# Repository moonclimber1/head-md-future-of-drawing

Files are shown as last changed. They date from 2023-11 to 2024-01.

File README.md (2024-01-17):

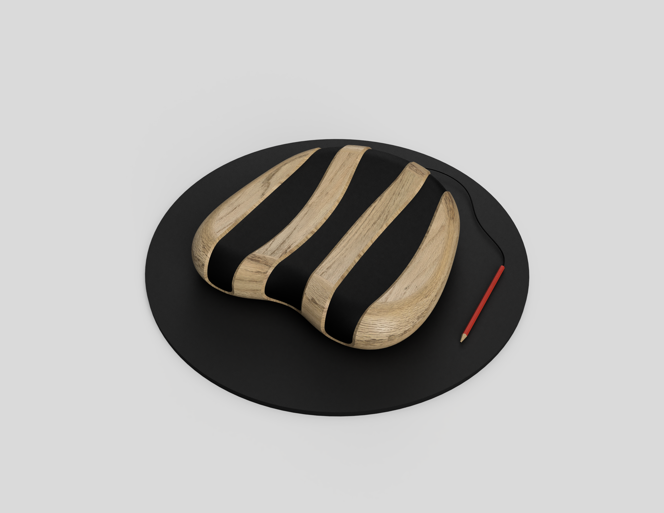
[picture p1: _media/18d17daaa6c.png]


# Future of Drawing

Github repository documenting process and code of the *Atelier Media Design 2023* at HEAD in which we explored possible Futures of Drawing in collaboration with Caran d'Ache.

[Overview of all projects of the class](https://github.com/HEAD-MasterMediaDesign/head-md-future-of-drawing)

## Shortcut Links

1. [Process Logs](process)  
   Logs every one or two working days
2. [To-Do-List](process/To-Do-List.md)  
   Current Tasks
3. [Presentations](presentations)  
   PDFs of all presentations did during the development process
4. [Form](form)  
   3D Renderings, Shape / Material experimentation
5. [Sound](sound)  
   Sound experimentations
6. [Electronics](electronics)  
   Arduino / Electronic diagrams and code
7. 

## Project Desription

**Resonance** -  Finding the inner balance through the movement of drawing

In the contemplative drawing experience Resonance people are  
encouraged to pause, slow down and enter a state of reso-  
nance - physically within the installation as well as metaphori-  
cally with themselves.

The core of the installation forms a novel interpretation of a  
sound bowl, crafted from wood and graphite. By engaging in  
slow rhythmic pencil movements on the object, people can set  
suspended pendulums in the space into gentle motion, creating  
contemplative soundscapes.

The rich electromagnetic properties of graphite are used to  
sense the rhythmic movement, allowing the pendulum to re-  
spond only when individuals move in resonance.

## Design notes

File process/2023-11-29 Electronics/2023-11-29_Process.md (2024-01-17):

# 2023-11-16 Process

## Electronics

In the last three days we had the electronics introduction with Pierre Rossel. We learned the basics of electronic circuits and arduino programming. After the obligatory basic examples of the first two days (dimming LEDs, potentiometer input, piezo, etc.) I started with my first own electronic experimentations today.

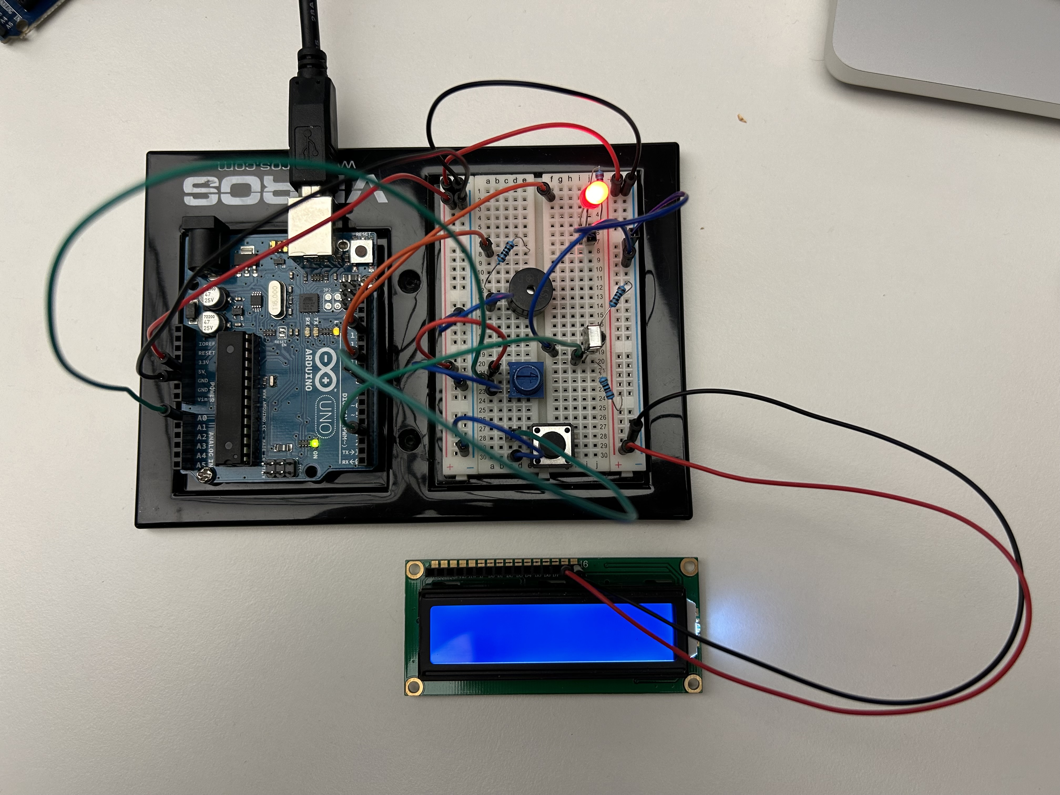
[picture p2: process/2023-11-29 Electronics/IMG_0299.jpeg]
Organized cable chaos on my breadboard
  
Organized cable chaos on my breadboard

Firstly I tried out different components of my arduino starter kit. I had an remote control and an infrared receiver and got them working together with the help of an downloaded online library. I made an setup in which I can remotely turn an LED on or off. Next I looked into the details how to get an display working. However as there is a lot of wiring up required (over 12 pins for my LCD display) I stopped with this endavour for time reasons. But at least I generally know how to do it in case I will need it.

**Video**  
[Video of LED Remote Control](IMG_0301.mov)

I wanted to move to doing actual experimentation that is related to my concept. After some wiring and tweaking I've got a resistance measurement on my pencil working. With this setup I am able to draw on a metal plate and it gives me the resistance value of the graphite which depends on the pressure. As a next step I created a TouchDesigner sketch to read the serial value and try around a bit with different signal processing options, e.g. applying lookup tables, filters, or lags. I achieved a setup in which I can control the brightness of my laptop screen just by changing the pressure with the pencil. The next step will be to use this improved clean signal to try to generate sounds. I started watching Max Msp Tutorial for synthesizer sound creations. With this setup I will hopefully soon be ready to do more user tests.

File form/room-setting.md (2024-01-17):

# Room Setting

**Carpet Measurements**

140cm x 130cm x 2cm

**Meditation Cushion**

35cm Diameter

17cm Height

**Projection Wall Distance**

1.7m Distance (equals 1.7m height)

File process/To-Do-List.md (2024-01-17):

# TODOs

## Current

**Object**

- [x] <span style="color:rgba(244,63,94,1)">Send improved 3D Model to Fred!</span>
- [x] <span style="color:rgba(244,63,94,1)">Send model to Laure</span>
- [x] <span style="color:rgba(244,63,94,1)">Produce Pencil Attachement</span>

  ***

- [ ] Prepare wood cover & holes for cables
- [x] Dremel missing cable channels
- [x] Sand edges
- [x] Glue parts together
- [x] Sand it
- [ ] Laquer it
- [ ] Sand strips
- [ ] Put graphite
- [ ] Cables (screws & routing)
- [ ] Put Electronics

**Room Setting**

- [x] <span style="color:rgba(244,63,94,1)">Design table & box</span>
- [x] Produce table
- [x] Produce equipment box
- [ ] Produce speaker stands
- [ ] (Design floating objects)

**Sound Design**

- [x] Check speakers & Interfaces
- [ ] Learn Ableton
- [ ] OSC Connection to TouchDesigner
- [ ] Create interactive soundscapes

**Visuals**

- [ ] Create Touchdesigner Visuals

**Presentation**

- [ ] <span style="color:rgba(244,63,94,1)">Deliver first version of presentation!</span>
- [ ] Define Framing!

**Electronics**

- [x] Fritzing wire diagram
- [ ] <span style="color:rgba(244,63,94,1)">Breadboard test</span>
- [ ] <span style="color:rgba(244,63,94,1)">Solder everything</span>
- [ ] Prepare for assembly

**Git Log**

- [ ] Look into git logs from class and last year
- [ ] Write more about design process / xylophone etc.

**Material to buy**

- [x] Clear lacquer / varnish spray
- [x] 6 nice screws for object
- [ ] (white wires?)
- [ ] female arduino connectors
- [x] Glue for cables
- [x] Round wood sticks

## Old

- [x] Research into different instruments (traditional, mechatronic)
- [x] Resarch into shapes (Exhibition tables, altar)
- [ ] sound design, electronics
- [x] metal workshop material measurement
- [ ] 3D Modeling
- [ ] form sketching
- [ ] try out lights

Define oscillating objects

- [x] research into different movement forms (springs, pendulum, unidirectional)

Define interaction & electronics

- [ ] usertesting
- [ ] Touchdesigner / P5 prototype

Think further

- [x] Think of flying object made out of paper (more related to drawing)
- [x] Email Audio Equipment
- [ ] Soldering excercise
- [ ] Try out Neopixel Rings
- [ ] Decide on camera model for documentation (sony pxw z150 vs canon 5D mark 4)
- [ ] ~~order pulleys~~
- [x] Frederic anschreiben
- [x] Pablo Audio Interfaces ausleihen & testen

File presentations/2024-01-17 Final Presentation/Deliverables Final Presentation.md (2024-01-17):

# Deliverables Final Presentation

Presentation until Wednesday

Fusion 360 File also until Wednesday

Github until Thursday morning

**General presentation**

November: What is the current state

January: -> This is the project!

Present as for someone new, but focus should lie on final product. 

Discuss process  but more as something that leads the way to the final product.

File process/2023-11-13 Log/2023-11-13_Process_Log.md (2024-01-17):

# 2023-11-03 Process Log

Today: Input with Laure, Brainstorming and discussions

After some discussion wth fellow students I feel the urge to revise my concept / experience again.

It might be more interesteing to focus on graphite as material in general instead of envisioning it in the form of a pencil.

Maybe create special analoge drawing devices that dont look an feel like penclis, maybe use eraser instead.

Maybe drawing with a pencil is too rigid for this contemplative experience, maybe graphite powder could be more interesting.

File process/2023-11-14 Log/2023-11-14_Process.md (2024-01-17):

# 2023-11-14 Process Log

I was not yet so happy with my concept and did a more research today and discussed the ideas with different persons.

My main problem was the following
“The more I add technological stuff the more it takes me away from being grounded ”

## Notes from discussion with Pablo

- There is nothing preventing you from being grounded if you do a simple interaction
- maybe also think of binaural sound via headphones instead of a big room setting
- do an simple satisfactory interaction that can help people relax and feel grounded  
  -> First goal: Relaxing people -> might eventually lead to being grounded
- finding inner balance through gesture of drawing
- constraining the movement you can do with a pencil might be interesting.
- #satisfaction: Inspired by wholesome videos that can help people relax
- Zen-like experience
- maybe draw in sand or graphite sand
- why do I want to use sound? -> it's an important aspect in relaxing people, immediate mental response
- feel good.
- also important to find sound references for the presentation

## New experiments

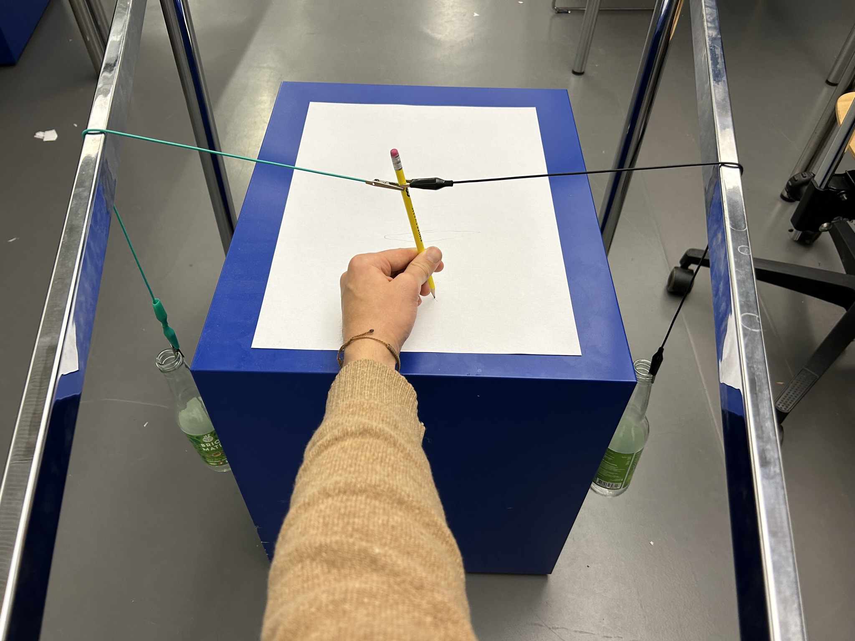
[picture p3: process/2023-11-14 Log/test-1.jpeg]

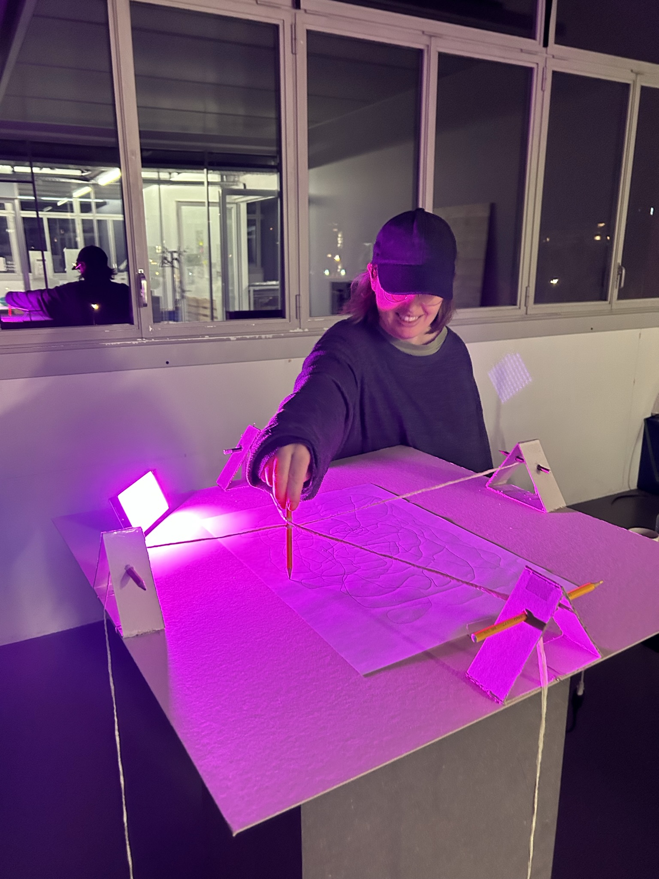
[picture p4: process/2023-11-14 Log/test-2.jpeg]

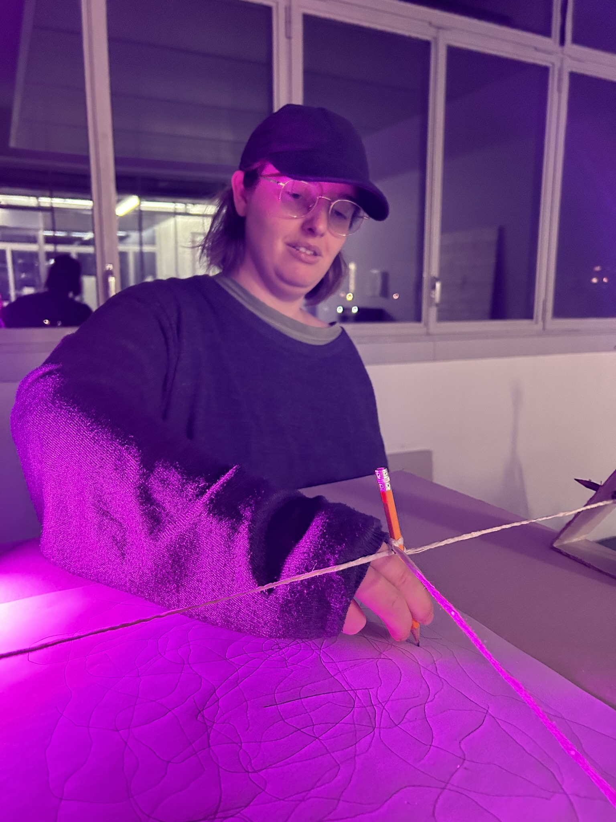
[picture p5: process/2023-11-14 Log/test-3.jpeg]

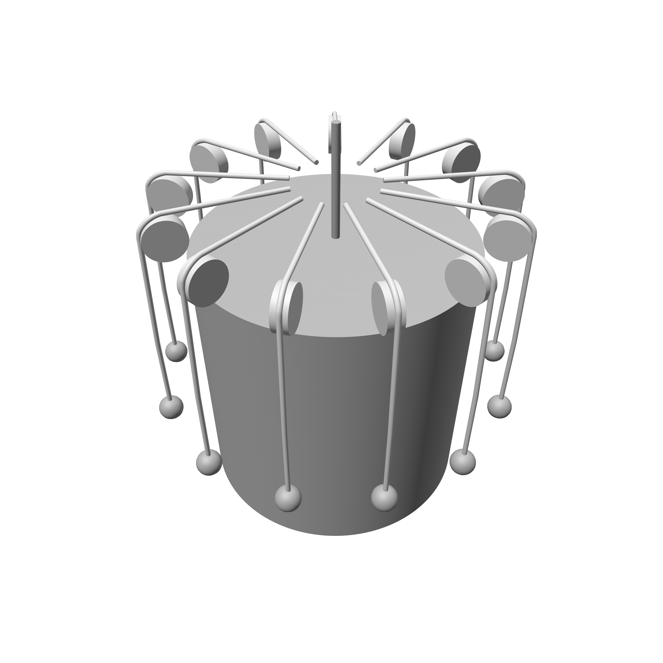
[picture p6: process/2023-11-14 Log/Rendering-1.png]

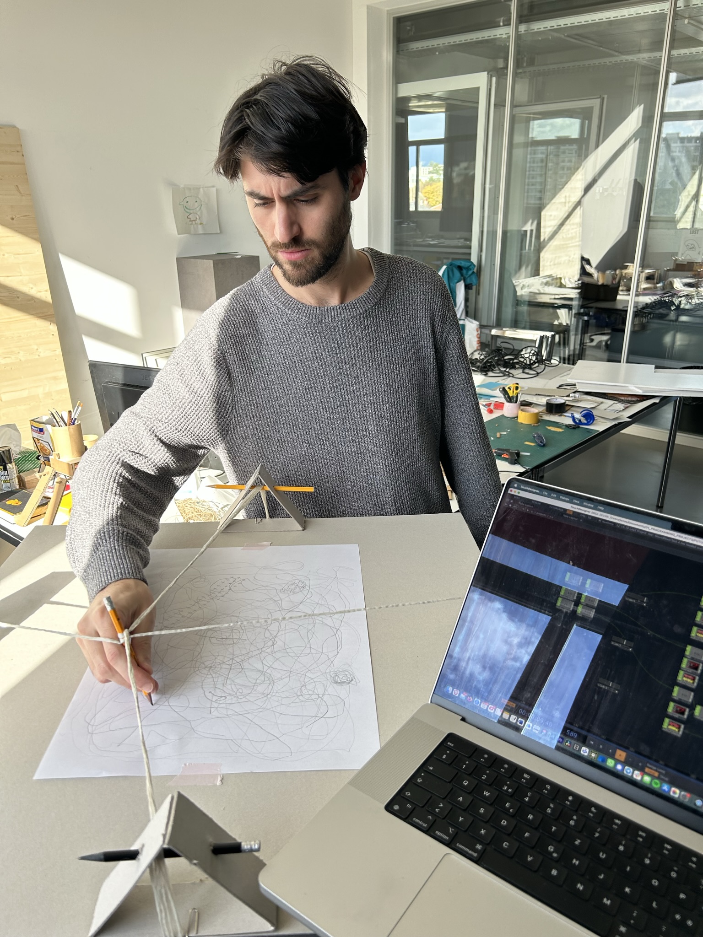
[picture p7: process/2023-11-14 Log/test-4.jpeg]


### Testing

People not only interact with the pencil directly but also try to pull on the ropes and draw indirectly over the mechanism.
Because of the big size of the object will probably also try to interact together with it.

I don't really want this indirect manipulation as it draws people away from what should be the focus. Maybe the ropes and stones have to be inside the table (behind a plexiglas) to not let people interact directly.

Through the constraints people are less likely to do figurative drawing, however they are strongly influenced about what has already been drawn. Ideally you wouldn't see a drawing on the paper and it would totally covered by graphite. Or you write on a metal plate.

## Updated Pitch

The project creates a multisensory contemplative drawing experience, with the goal of relaxing and centering / grounding people. They interact with an mechanical drawing object that at the same time gives constraints and sparks satisfaction through movement. While drawing, electromagnetic measurements of the graphite scratching on the the surface are measured and transformed into sounds that are altered by an AI to create looping spheric relaxing sounds. The installation creates a feedback loop in which the person influences the soundscape through their drawing movements while at the same time the sound influences their drawing.

There is an feedback loop between the object doing sound influencing the person and the person changing the sounds.

 you draw to create sounds while at the same time being influenced by the sonic expeirence and the Ai

In this manner a feedback loop is created

sparks satisfaction

designed to give constraint

an satisfactory experience

 an assists people in their groudning process. 

The pepople interact with an 

The drawing device is designed to makee people mre focus on the movemtents and have a visual feedback of the 

 make the the experience more satisfactory. 

cons

visitors interact with an satisfactory object while an AI creates sounds 

AI creates a sound that lets the come into resonance with their boday 

helping people to ground themselves and relax

helping people to find inner balance / center themselves / 

I wanted to design an object or experience that grounds people through the action of drawing.

There is an feedback loop between the object doing sound influencing the person and the person changing the sounds.

Where is the AI?

Finding resonance, findoing something that resonates with people

in the best case they get so focussed that they enter a meditative zone

binarual sound headphones

The project creates a multisensory wholesome / relaxing / contemplative drawing experience.

What is the title?

What is the core idea?

The project creates a multisensory contemplative drawing experience in which the electromagnetic traces of graphite are used to create a meditative, slowly pulsating painting of sound that gradually evolves in co-creation with an AI. The experience starts in a puristic setting of a dark room which floor is covered by water and only features a pencil hanging down from the ceiling and a blank canvas on the wall. Visitors have to enter barefoot and alone. Inspired by the slow rhythm of meditative breathing as well as the analogue richness of graphite, a pulsating and looping spheric soundscape starts to form as soon as the person begins drawing. Every drawn line contributes a sound to the evolving live loop while the AI is altering the past patterns with time. Visitors are encouraged to go with the flow as the emphasis shifts to the mental impacts of the act of drawing while the specific content of drawings becomes irrelevant.

Presentation peparation

- Go straight to the core of your project
- In interaction design you can not fake it last minute, you need to take your time and constantly test

This project is a ...

go straight to the point
put sentence of the end to the beginning.

help peole feel grounded

User Journey,

put pictures / vidoes of research / tests.

very simple shape research

if you have insights / discoveries from field reseach put those discoveries.

User tests: What worked?

go to very essence!

The testers expected…

First image: sketch, hand drawn.

Sound inspo
https://www.youtube.com/watch?v=8V71sATDTqs
https://www.youtube.com/watch?v=6BM-7oG1W6Y

## User Journey

1. Visitor gets curious about that special object.   

out of curiosity user wants to try out object 

User recognizes sound reactivity 

2. Visitor starts drawing with pencil and recognizes sound and watches rocks going up and down.
3. Visitor puts on headpohones and
4. 

is attracted by object and starts to try it ot

experiment of sound, graphite and metal (& movement)

pencil graphite loop

what gives it to me?

need an information

music is guiding me 
not enough guided

im getting into the flow
being out of sync

you have to get into their groove to get into your groove (like with a cat)

harmonics resonace is an interesting concept to be furter explored. Through drawing finding your resonance

rez game

can be honest about stuff Im not happy about yet, don't have to sell

its missng a conclusion, so what?

replace paper, put metal plate or dark paper. 

It need some kind of feedback, maybe get more into resonance 

talk shortly about voltage pencil experiment.

in the experiment

Is it more than just fun? Oh that's nice? What should stick?

It is an 

## Presentation notes

I was focussed on intensified sensory drawing experience and grounding people. as well as graphite 

talk about grounding research

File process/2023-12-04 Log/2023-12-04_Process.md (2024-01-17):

# 2023-12-04 Process

Today I further refined my concept. I had feedback discussions with Laure and Douglas as well as people of the class. 

## Discussion with Laure and Douglas

- Prototype is looking great, no need for the ropes (only if needed for the position, but there are probably better ways)
- Pencil pressure and drawing acts as a distortion to the sound
- around 4 instruments (e.g. gongs) hanging in the back, which are triggered by the movement of the pencil

- hanging things is hard, also think about other ways
- does it need to be a physical gong? It can be a modern interpretation of a gong, for example a physical object that resembles it while the sound is digital. Or just a specially formed resonance body for a speaker. Or cones, or a minimal paper shape, etc. 
- metal plate might have different zones for different sounds similar to DJ pults or drum machines. Zones might for example be achieved by thin laser engravings.
- A speaker with cones can already be very interesting, does not have to be a physical instrument. 

## New Inspiration

I discovered an artist called Lotta Stoever with interesting works which I found inspiring for my project.

https://lotta-stoever.net/works/towards-an-intimate-electricity

https://lotta-stoever.net/works/indisposable

## Temporary Materials List (rough)

- Instruments (Gong)
- Motors
- Metal Ropes
- Metal wheels
- Lights
- Microphone feedback

## Discussion with Ares

- currently difficult to decide what exact instruments I want to place with which visitor can inderectly interact with through the pencil movement
- I am missing one keyword that helps me connect the dots, to know better what I want as the output. Keyword might be something like "contemplative" or "oscillation" for example
- think also about big body movements
- doesnt have to be a horizontal metal plate on a table, can have any 3-dimensional form 

## Discussion with Laure

- maybe unidirectional drawing movement doesnt fit grounding experience so well
- think of more abstract objects going up and down, can be more poetic
- can also be a turning object or pendulum, or windmill like

## Next steps

I created a To-Do-List to track my progress and have an overview of my next steps:

[Link to To-Do-List](../To-Do-List.md)

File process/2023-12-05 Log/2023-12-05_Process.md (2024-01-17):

# 2023-12-05 Process

The interaction as well as the link to the "instruments" got much clearer today. I consider the keyword "Resonance" as the main keyword for the installation. "Resonance" can be interpreted in a metaphorical way, e.g. finding your inner resonance / get grounded as well as in a physical way for the interaction. Inspired by the mechanics of a pendulum or swing the goal is to make pencil movements in a specific rhythm to get into resonance with the oscillating floating objects which are hanging in the back. Similar to a physicial pendulum you can not just apply force at any time, you have to find the right moment to get the pendulum oscillating. The movement of the three pendulums will then influence the sound.

Resonance explained:  
https://www.youtube.com/watch?v=MIgQrHW53Lw

Example of dependence on the right rythm to get the pendulum into motion:
https://youtu.be/MIgQrHW53Lw?t=256

## Electronics Discussion with Pablo

- will neeed stepper motors with driver (never use the bad tb6600 model!)
- go at metal workshop and measure all kind of materials for different resistances
- maybe hack new carbon support printer
- cable thickness matters. when dealing with low voltages you have to be careful to no put to much current onto the cables. Check for max Ampere per length rating. Otherwise they will start burning.

## Discussion with Laure

- Circular movement is beautiful
- up and down movement is fluid as long it is on a big area, long plate might constrain this
- however circular movement maybe more difficult in terms of interaction
-

-
- light objects, like feathers, plastic foil, which make movements through going up and down and can also make waves if moved fast
- floating jellyfish
- rounded fluid forms

### How to find object design references online

- Pinterest & pinterest similar recommendations (maybe seperate account to train algorithm)
- if something sparks interest find out artist and search for more work of them
- Collection of interesting artists / design studios
- Wallpaper & Deezen Magazine
-
-

Ideas reasonating through light instead of movement

## Inspiration

Interesting kinetic light installation:
https://www.behance.net/gallery/141180655/Kinetic-Light-Installation

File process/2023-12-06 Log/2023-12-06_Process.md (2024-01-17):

# 2023-12-06 Process

made experiments with conductivity
carbonfiber plate experiment

electric field sensing

3D modeling & questions answers

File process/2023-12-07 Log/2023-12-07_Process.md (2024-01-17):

# 2023-12-07_Process

Douglas Testing Day Intro
Douglas Electronics Discussion

What I did:
- Electronics List, read into different technical topics to understand which exact components I need

Floating Objects Prototypes Results
- idea of having an inner glowing object and some kind of structure aroung
- the slow speed that I am targeting will not make plastic foil move on their own
- maybe strings attached to plastic foil
- maybe big paper wave or similar
- paper might still be interesting because of the relation to caran d ache

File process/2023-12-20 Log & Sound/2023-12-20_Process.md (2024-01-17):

# 2023-12-20 Process

Today I worked on the 3D Design of the product as well as organized sound equipment for january.

## Discussion with Laure about 3D Model

New inputs and references on how I can go for a warmer and more rounded form for the structure.  
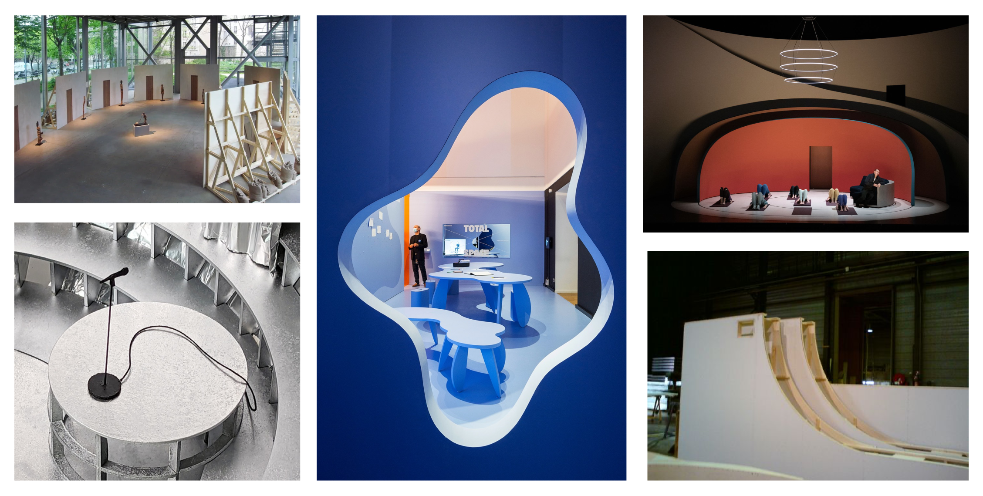
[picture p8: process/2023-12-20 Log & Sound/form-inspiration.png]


## Sound Equipment

Asked for sound equipment in pool image son. Difficult situation as there are jury presentations at the same time in January.

I reserved the following items in de magasin audiovisuel:

- 3 Fostex Speakers starting from the 10th of January
- Cameras (either sony pxw z150 or canon 5D Mark IV) starting from 16th of January for Documentation + Canon 16 -35mm lens	

Speaker stands still unclear

For the sound cards I might combine two sound cards from Media Design. Have to test how well that works.

granular synthesis

either only max msp + vsts

sampler, granular, synth, sample-based

VST: Noire grand piano (Native instruments)

note 1-12 or note 1-24 (maybe multiplied or add 12)  
first generating random node, and then use scale

Slide AI for May

note in chromatic scale  
random within a collection of possible scale

anneroli

put keyboard on computer

some things evolve over time

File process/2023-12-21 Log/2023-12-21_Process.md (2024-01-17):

# 2023-12-21 Process

## Feedback Laure Douglas

back to the basics  
graphite plate is the important thing.  
Too much structure draws away from the center of the poetic interaction.

projection as a plan B if physical movement doesnt work out until January presentation

Focus more on Design of the interaction plate object! Its at the center of my project and corresponds more to what others are doing as well.  
Get this object poetic in itself

pencil design second / third priority

paper is nice as floating object

arms that go up and down probably much better than undwindig. Also has poetry to it

Xylophone: Put two sticks below and its already regarded as a xylophone I can play with.

its nice to see cables and also nice to see inside

Prototype Plate is beautiful!

box design not ideal, same as with structure. It draws away from the poetics, feels not inviting enough to interact with.

Get rid of structure again. Mount all motors up to the ceiling.

Inspiration Alexander Calder  
Zimoun / Pelong Ref

why not go about projection

They are happy with paper material of floating object

In case of the floating objects, nice floating is more important than the look, therefore its good to test out material first and then do the form.

Plexiglass see through

maybe even make electronics / arduino visible with a little light? maybe too much? How technical I want it to be?

has to be discussed how importan ergonomics really are.

Critique current interaction console: You would no put your hand ther while drawing. It has to be the big angled plate / table so it works

maybe visible cable connection to object?

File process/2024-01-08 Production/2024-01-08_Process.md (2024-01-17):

# 2024-01-08 / 09 Process

Morning Appointment with Frederic in the atelier prototypage for the CNC. He will be able to produce the object but unfortunately only short before the presentations.

## CNC Specifications

- 4cm maximum piece height
- 4cm means a minimum radius of 3mm when doing concave edges
- I will have to cut my object into pieces, as the CNC only works on 3 axis
- 12mm distance between objects, 5mm to the edges
- Max working area 1000mm x 500mm
- one round drilling tool and one flat tool
- if its only on the surface its possible to work with thinner tools

## Work

3D Modeling & Troubleshooting with Laure

Wood workshop organizing

Wall projection test

## Wood Choices

Volume for CNC: 412mm x 824mm x 43mm = 1'4597'984 mm3 = 0,014 598 m3

**Wood Options**

| French | German | English  | Hardness | Price m3 | Object Price |
| --- | --- | --- | --- | --- | --- |
| <span style="color:rgba(156,163,175,.8)">Epicéa</span> | Fichte | Spruce | Soft | 1782 | 26 CHF |
| ~~Pin~~ | ~~Kiefer~~ | ~~Pine~~ | Soft | | |
| Hêtre | Buche | Beech | Hard | 2558 | 37.35 CHF |
| Erable | Ahorn | Maple | Hard | 3218 | 46.97 CHF |
| **Frêne** | Esche | Ash | Hard | 2558 | 37.35 CHF |
| Chêne | Eiche | Oak | Hard | 3713 | 54.20 CHF |

**Hêtre - Beechwood**

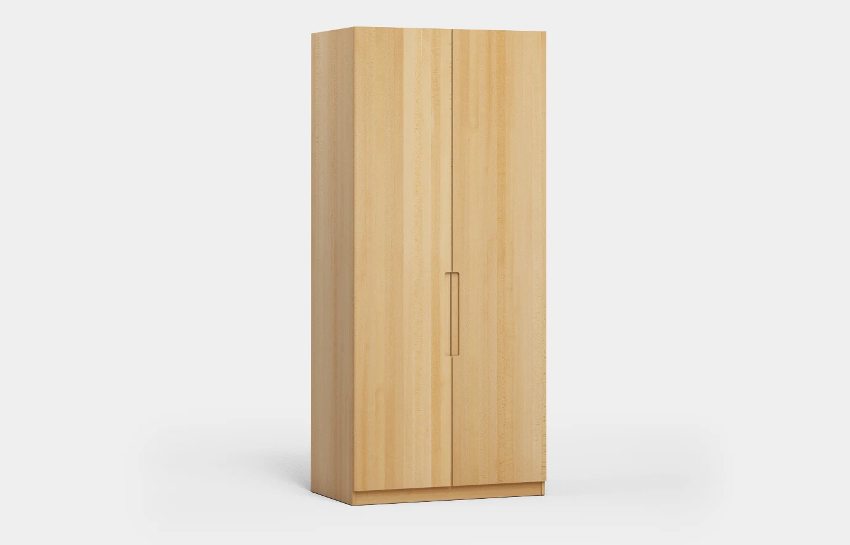
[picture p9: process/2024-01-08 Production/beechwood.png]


**Frêne - Ashwood**

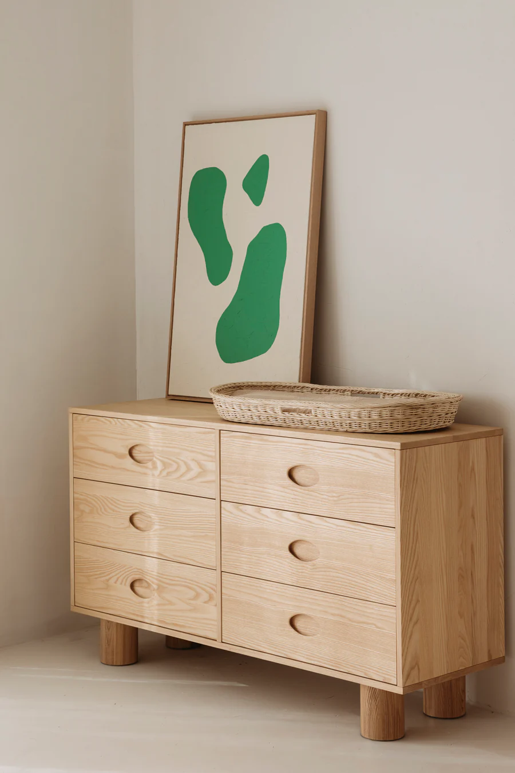
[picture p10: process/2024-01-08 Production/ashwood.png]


After some comparison I decided to go with ashwood (beechwood as a backup If they dont have enough) Together with beechwood its the cheapest of the hard wood and has a nicer look and better stability than spruce wood.

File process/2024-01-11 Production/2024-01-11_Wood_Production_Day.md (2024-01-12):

# 2024-01-11 Wood Production Day

The plan for today is to produce the following objects in the wood workshops:

- [ ] Glued Ashwood Block for CNC milling
- [ ] MDF Table
- [ ] Speaker stands
- [ ] Computer box
- [ ] Pencil cap

Additionally (if time) search for the following objects:

Unfortunately I could not produce anything and had to wait the whole day as he was occupied with other projects.

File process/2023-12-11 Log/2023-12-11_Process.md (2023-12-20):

# 2023-12-11 Process

Today we had an soldering introduction with Pierre.

I started to research into how I can electronically amplify my measured signals to be able to measure with greater precision. For the amplification I need so called operational amplifieres (either simple gain configuration or used as a difference amplifier).

With the help of Pierre I was able to design a first amplification circuit in Fritzing as well as on my breadboard.

I use an LM358P integrated circuit for the amplification.

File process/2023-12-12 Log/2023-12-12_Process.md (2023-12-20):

## 2023-12-12 Process

Today I continued working on the circuit design and data processing.

To calculate the different values of the circuit I hat to do a lot of mathematics. Together with Pierre we found an 6 terms equation system for 6 unknowns that we solved together. 

I found out that now matter how much I tried I couldnt get the carbon fiber plate working to get usable values. I will have to switch to just using an wood plate with pencil graphite on it. 

I tried to reserve an appointment in the wood atelier but failed because they were in a hurry and had no time.

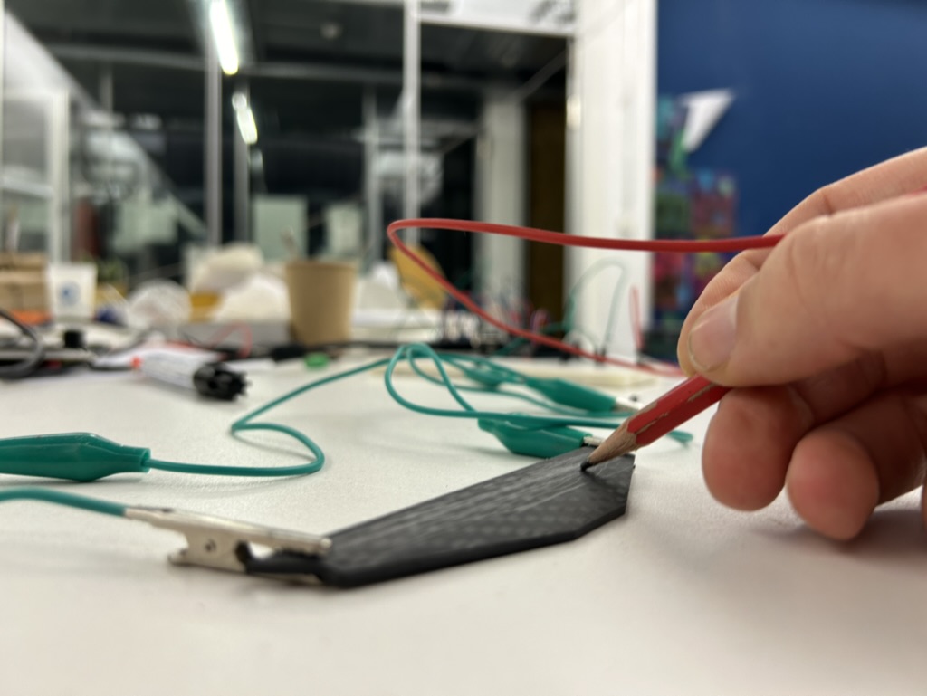
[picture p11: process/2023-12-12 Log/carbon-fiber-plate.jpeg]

Carbon fiber plate unfortunately not working. 

-> Picture

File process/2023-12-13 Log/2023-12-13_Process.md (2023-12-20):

# 2023-12-13 Process

Today I did different preperations for the testing day.

- I built the interaction plate by using a wood plate and painting it with pencil graphite. Screws for a better conductive connection.
- Coding of the Spring movement (Combination of Touchdesigner and Node js, communication over OSC)
- Preparing my research questions for the testing.

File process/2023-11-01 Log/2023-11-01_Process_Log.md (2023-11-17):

# 2023-11-01 Process Log

Today I went on with my two previous ideas and did more experiments.

## 1 breath = 1 drawing
**Traces of breath**

Based on the first idea of having one drawing per breath and creating a medidative drawing experience I did some experiments with people of our class.

### Setup

Screen with slowly pulsing circle or headphone sound which set the rythm of inhaling and exhaling. 

After every breath cycle the participants get a new small piece of paper or a new white page on the ipad screen for their next drawing.

Instruction: It doesn't matter what you draw it's just important to focus on your breath and go with the flow. 

Very simple p5.js Code for the pulsing circle:

```
function setup() {
  createCanvas(800, 800);
}

function draw() {
  fill(220,220,220, 255);
  rect(0,0, width, height)
  noStroke()
  fill("blue")
  circle(width/2, height/2, map(sin(frameCount * 0.0075), -1,1, 300, 500));
}

function mousePressed() {
  fullscreen(true);
}

function windowResized() {
  resizeCanvas(windowWidth, windowHeight);
}
```

Link to the audio with the guided breathing meditation  
https://www.youtube.com/watch?v=N0tY-TaEEQI

### Findings

- Calming / Relaxing experience
- People stop thinking about the drawing and get into a flow
- Drawing can help to prevent thoughts while meditating, but it can also draw away attention from the breathing
- natural to make one drawing movement for inhaling (often going up) and another drawing movement for exhaling (often going down)
- easier / more natural with eyes closed
- everbody does abstract movement

#### Experimentation Pictures

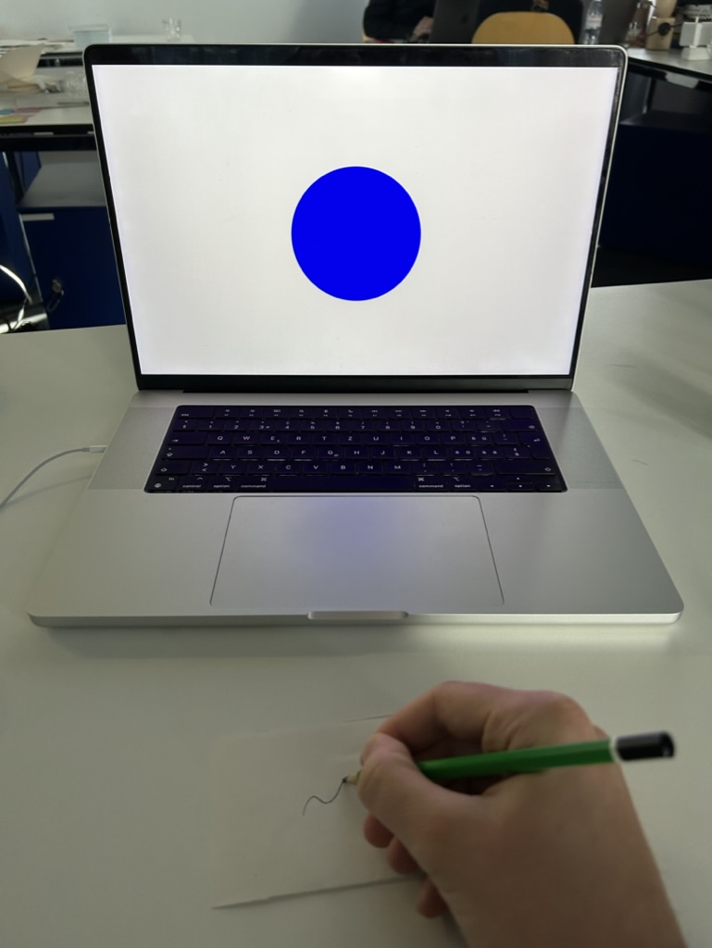
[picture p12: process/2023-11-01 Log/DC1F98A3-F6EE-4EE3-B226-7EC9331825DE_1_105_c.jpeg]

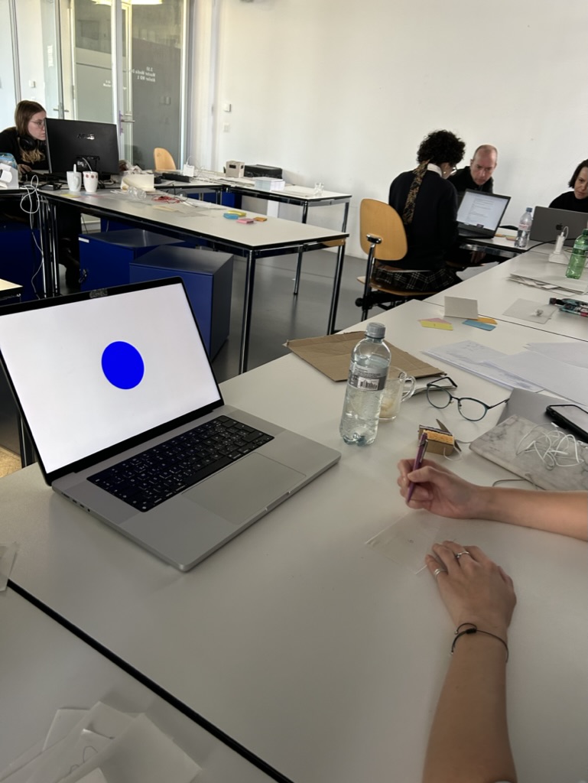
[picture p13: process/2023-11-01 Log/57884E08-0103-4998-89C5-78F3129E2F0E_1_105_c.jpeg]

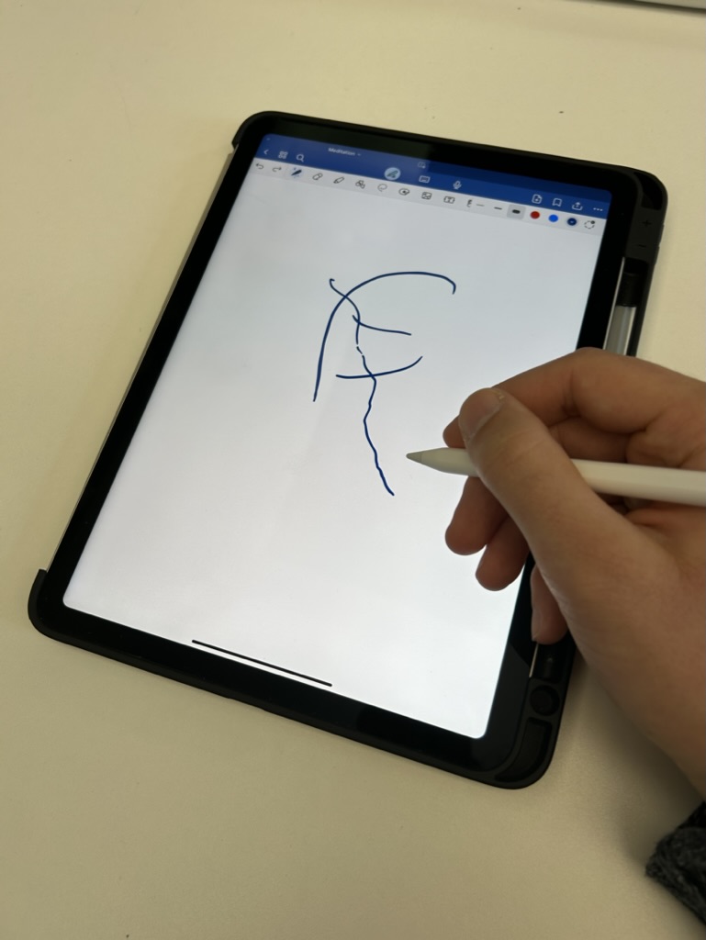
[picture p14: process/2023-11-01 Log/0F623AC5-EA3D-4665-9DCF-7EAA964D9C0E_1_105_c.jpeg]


## Pencil Conductivity

I found an interesting video from ElectroBoom on YouTube:  
https://youtu.be/5YBwDNfOaxU?si=ej5ED4wHxOc74gEq

The video showcases the electric conductivity of graphite (material of which pencil leads are made of). With graphite you can build potentiometers and make strokes and flames (graphite is even used in nuclear plants) or just use it as a simple conductor. I came up with the idea of connecting a pencil with a resistance sensor that can measure the electrical properties of your drawing while you create it and transforms this information into another medium. (e.g. sound, visuals, etc.)

Inspired by the video I tried to measure the electrical conductivity of pencil lines on paper. Unfortunately this only worked half. I only got measurable resistance if the line was done with a lot of pressure on the paper but not with a normally drawn line. 

However I found out online that harder pencils might work better. And appereantly you can build experimental instruments just from your drawings. 

https://makeymakey.com/blogs/how-to-instructions/sketch-it-play-it

#### Experimentation Pictures

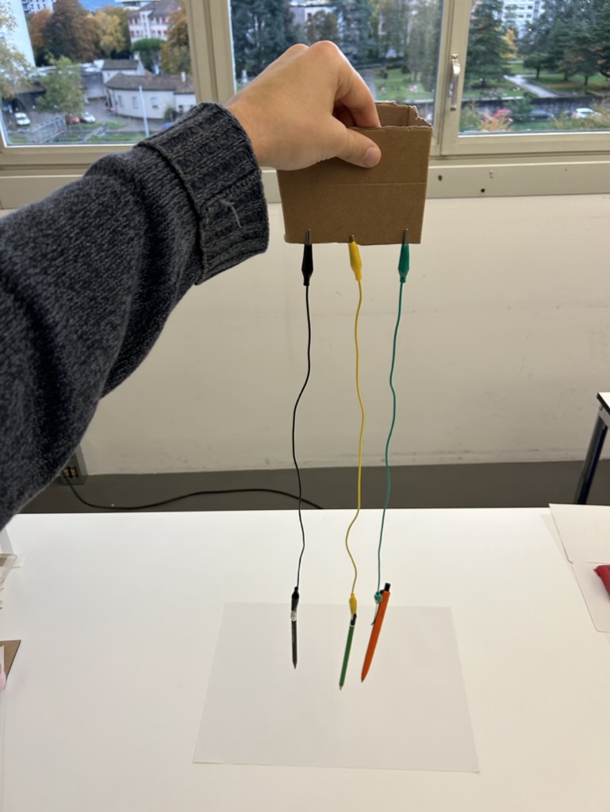
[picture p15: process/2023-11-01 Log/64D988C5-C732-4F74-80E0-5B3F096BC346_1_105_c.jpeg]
Conducting Pencils


## Feeback Meeting

**Idea 1 in 1 sentence:** Interactive meditative drawing experience in which one breath equals one drawing. 

**Idea 1 in 1 sentence:** Interactive experience making use of the astonishing superpowers of graphite.

**Interest idea 1:** personal interest in meditation

**Interest idea 2:** graphite superpower material, you can do every magic with it you can also do with electricity

**Feedback Meditation Idea:**
- Dont go down the the general mediation rabbit hole with mindfulness and similar stuff. Very whitewashed, commercialised practice. Even meditation apps. Very western. Find another angle to it. 
- If I do mediation focus more on the drawing and what it makes with the drawing.

**Feedback Superpower-Material Graphite**
- Play with the analouge properties of graphite. Don't try to make digital on off signals out of it like makey makey. 
- Keyword analouge infinite richness
- Different lenghts of pencils different characteristics

**Connecting the two ideas**

Being in the body with the help of graphite. 
Graphite has like analogue quality and richness to it and is similar to breathing.

Interesting reference (plays with the analogue properties)
https://www.waterlightgraffiti.com/about-wlg/

If I want I can still create an artificial breathing based on the drawing. 

Look out for things / habits that ground people. (doesnt have to be breath, can be ice water, elastic band, running, etc. )

Creating a feedback loop  
draw and measure at the same time, connected circuit with body (maybe tiny electroshocks?)

Make people be in their body, or not at all with the help of graphite.

draw to sync with your body

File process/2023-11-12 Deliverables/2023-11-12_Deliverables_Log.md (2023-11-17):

# 2023-11-12 Deliverables & Log

## Concept Pitch

The project creates a multisensory contemplative drawing experience in which the electromagnetic traces of graphite are used to create a meditative, slowly pulsating painting of sound that gradually evolves in co-creation with an AI. The experience starts in a puristic setting of a dark room which floor is covered by water and only features a pencil hanging down from the ceiling and a blank canvas on the wall. Visitors have to enter barefoot and alone. Inspired by the slow rhythm of meditative breathing as well as the analogue richness of graphite, a pulsating and looping spheric soundscape starts to form as soon as the person begins drawing. Every drawn line contributes a sound to the evolving live loop while the AI is altering the past patterns with time. Visitors are encouraged to go with the flow as the emphasis shifts to the mental impacts of the act of drawing while the specific content of drawings becomes irrelevant.

The concept idea draws from my research on mental grounding and meditation as well as my research on the hidden superpowers of graphite.

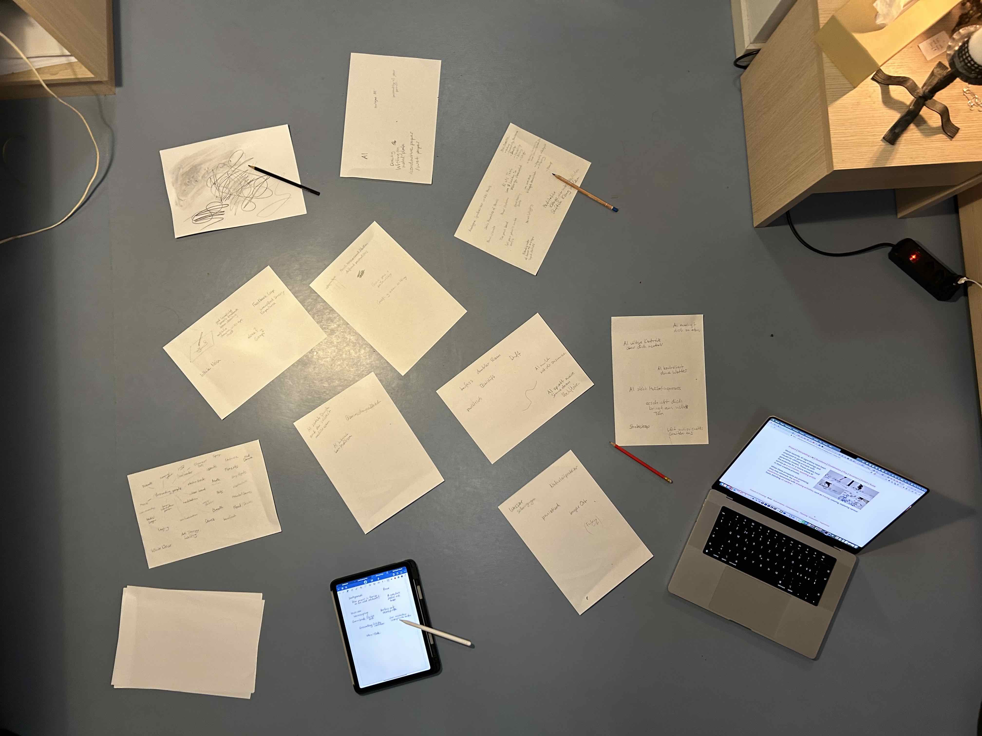
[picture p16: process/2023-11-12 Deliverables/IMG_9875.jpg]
Idea Brainstorming

Idea Brainstorming Session

## Research Key Insights

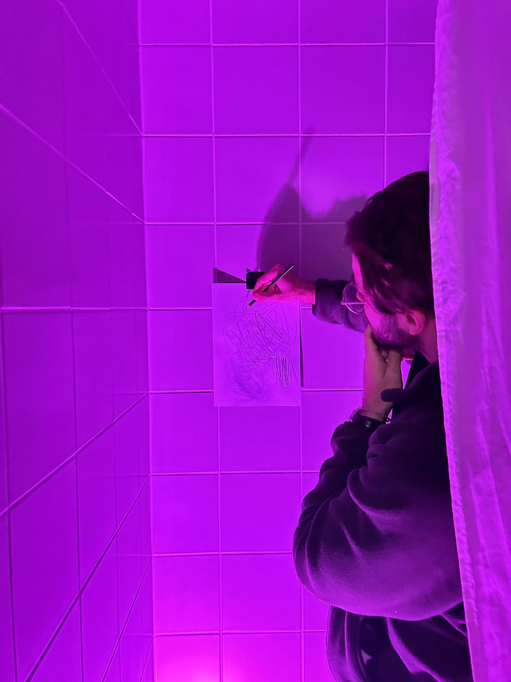
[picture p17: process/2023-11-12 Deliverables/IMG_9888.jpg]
Prototype Testing

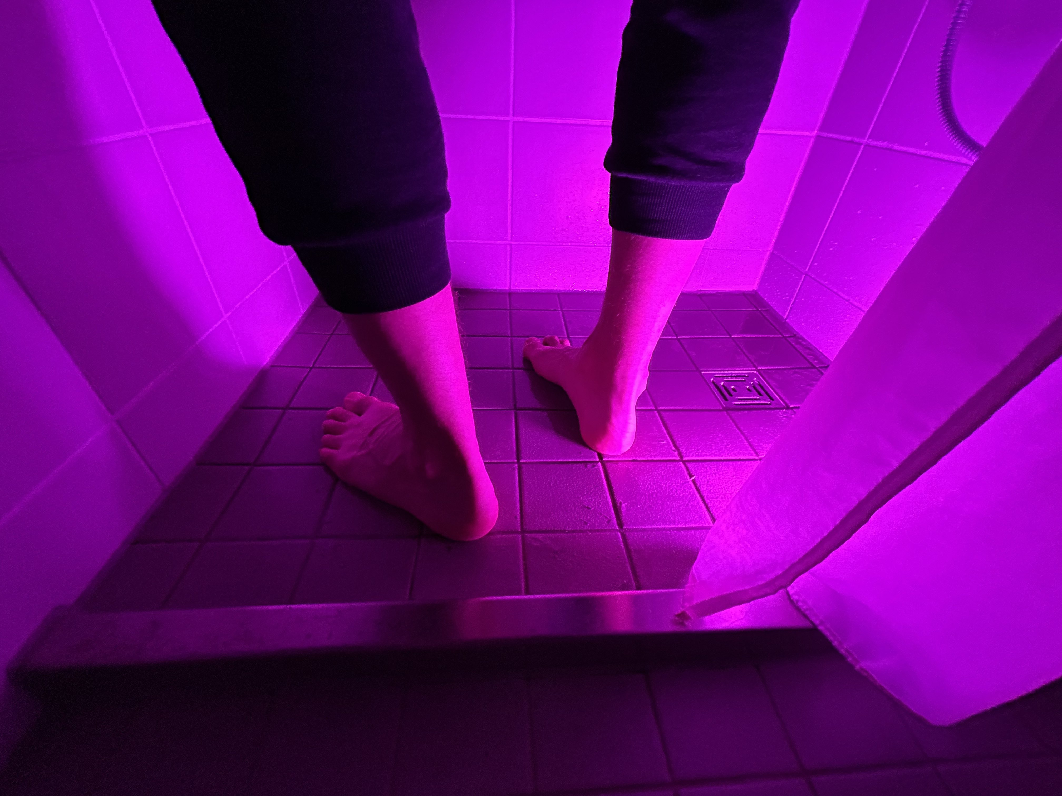
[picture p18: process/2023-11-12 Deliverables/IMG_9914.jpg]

Pictures from latest prototype testings with flatmates.

### Research on mental grounding and meditation

Quote from psychologytoday.com:

> Whenever you find yourself feeling anxious or stressed, you can use grounding techniques to reconnect with yourself and the present moment. This research-based strategy may be helpful for anxiety, panic attacks, flashbacks, or even dissociation.
> Grounding techniques work by “grounding” you in the present moment and pulling you away from intrusive thoughts or feelings. This refers not only to having your “feet on the ground” but also your “mind on the ground.” When you turn your attention away from thoughts, memories, or worries, you can refocus on the present moment (Fisher, 1999).

Grounding can help many people cope with their mental challenges. Grounding techniques are manyfold and and can include the following or more:

refresh with ice water, cold shower, bath, scents, music, white noise, running, snapping rubber band, touching specific objects, yoga/stretching, mental math arithmetics, small electro shock, laughing, meditation, slow breathing, sexuality, nature, mud, walking barefoot, pets, mental games, doing art,dancing, ...

I did experiments with people to try out grounding techniques. The first experiment was a more classic meditative experiment where people listened to breathing instructions and had to draw something with every breath. It was interesting to observe that after little time people started drawing abstract and focusing more on the movement than the drawn figure itself. The movement also helped them not to wander off with their thoughts while meditating.
For the installation I want to think more broadly about the topic of grounding and not only about meditation. However I found this slow rhythm of the breathing very interesting and want to build further on that.

In the second expirment, inspired by the current vision for the installation I asked flatmates to stand barefoot onto the wet floor of the shower and draw to a slowly pulsating sound and colored light. The combination of light, sound and water made for an enchanting experience even if not very long lived. After around 2 minutes it started to get uninteresting, but this could also be attributed to the fact that the drawing experience was not yet interactive and the sounds were static.

### Research about superpowers of graphite
The more I researched about the material graphite (which pencils leads are made of), the more fascinated I've got. Graphite is a superpower material that is used for a lot of different use cases. Here is a non comprehensive list what can all be done with graphite:

- Electric Arcs / Strokes / Flames
- Melt metal, even steel
- Diamagnetic Floating
- Conductivity
- Potentiometers
- Batteries
- Nuclear Plants: Moderator / shielding material
- can be turned into diamonds under pressure and high temperatures

Graphite has the interesting property, that the the electrical resistance of it changes based on the length or thickness of the material. Because of this property graphite is used in potentiometers which are at the heart of a myriad of analogue and digital input devices.

The fact that graphite is not only conductive but allows for continous changing of its electric properties, adds an analogue richness to the material that is interesting to be explored by sound. Ultimately a connection to analogue synthesizers can be drawn: Analogue synthesizers use reactive electronic components to create rich and warm sounds incorporating graphite potentiometeres as their main input and interaction technique.

Example video of using pencil graphite to modulate the brightness of an LED  
https://www.youtube.com/watch?v=aElHVTv-75M

In addition to the electromagnetic properties of graphite, there are more properties of the pencil that might be interesting to be explored in a sonic way.

- Hardness
- Density
- Length
- Pressure
- Flexibility
- Friction

## User Journey

1. Visitor enters dark room. There is only a dim pulsating light on the pencil which catches the visitors attention.
2. Visitor wants to try out that pencil, but doesn't want to get wet shoes and therefore decides to go barefoot.
3. Visitor tries out first strokes and perceives sonoric interactivity.
4. Visitor continues drawing and exploring.
5. As the lights and sound in the room are pulsating visitor starts to draw and also breathe in that rhythm.
6. Visitor perceives AI changements to the former sounds.
7. Slowly sound and light gains momentum.
8. After about ten minutes sounds are calming down.
9. Visitor slowly leaves the room and feels grounded in the best case.

## Tentative conclusions

### Next steps

Some technical questionmarks whether measuring works in that form as envisioned. Needs technical testing.

Do more user tests with more functional prototypes. Do experiments including interactive sound.

Feedback Sound Loop

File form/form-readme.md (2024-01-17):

# Form

## Part List

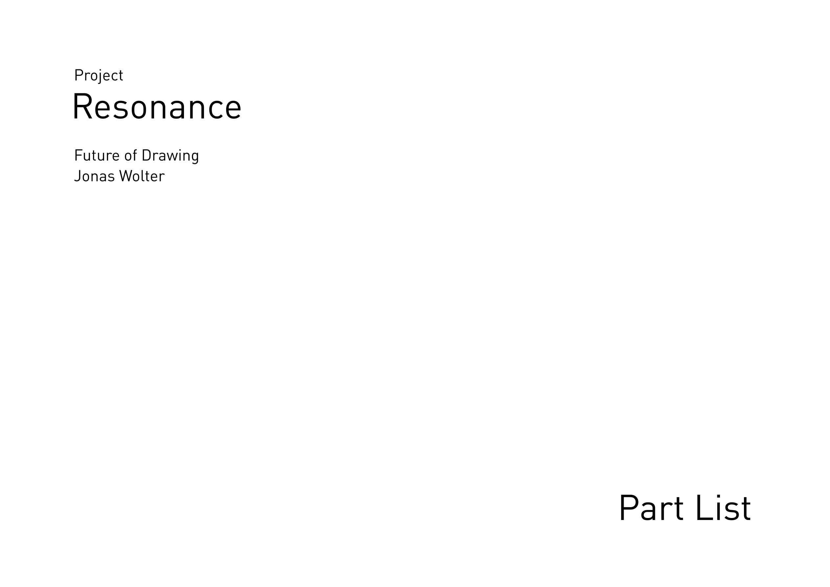
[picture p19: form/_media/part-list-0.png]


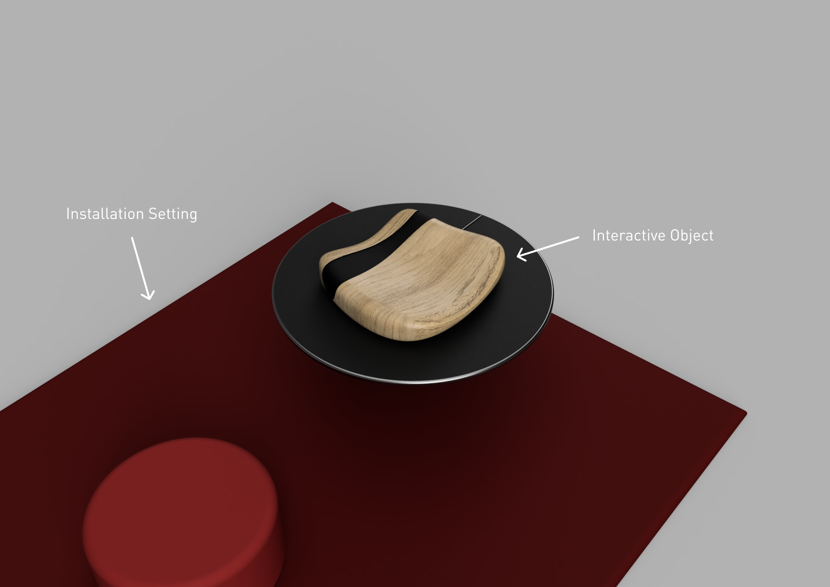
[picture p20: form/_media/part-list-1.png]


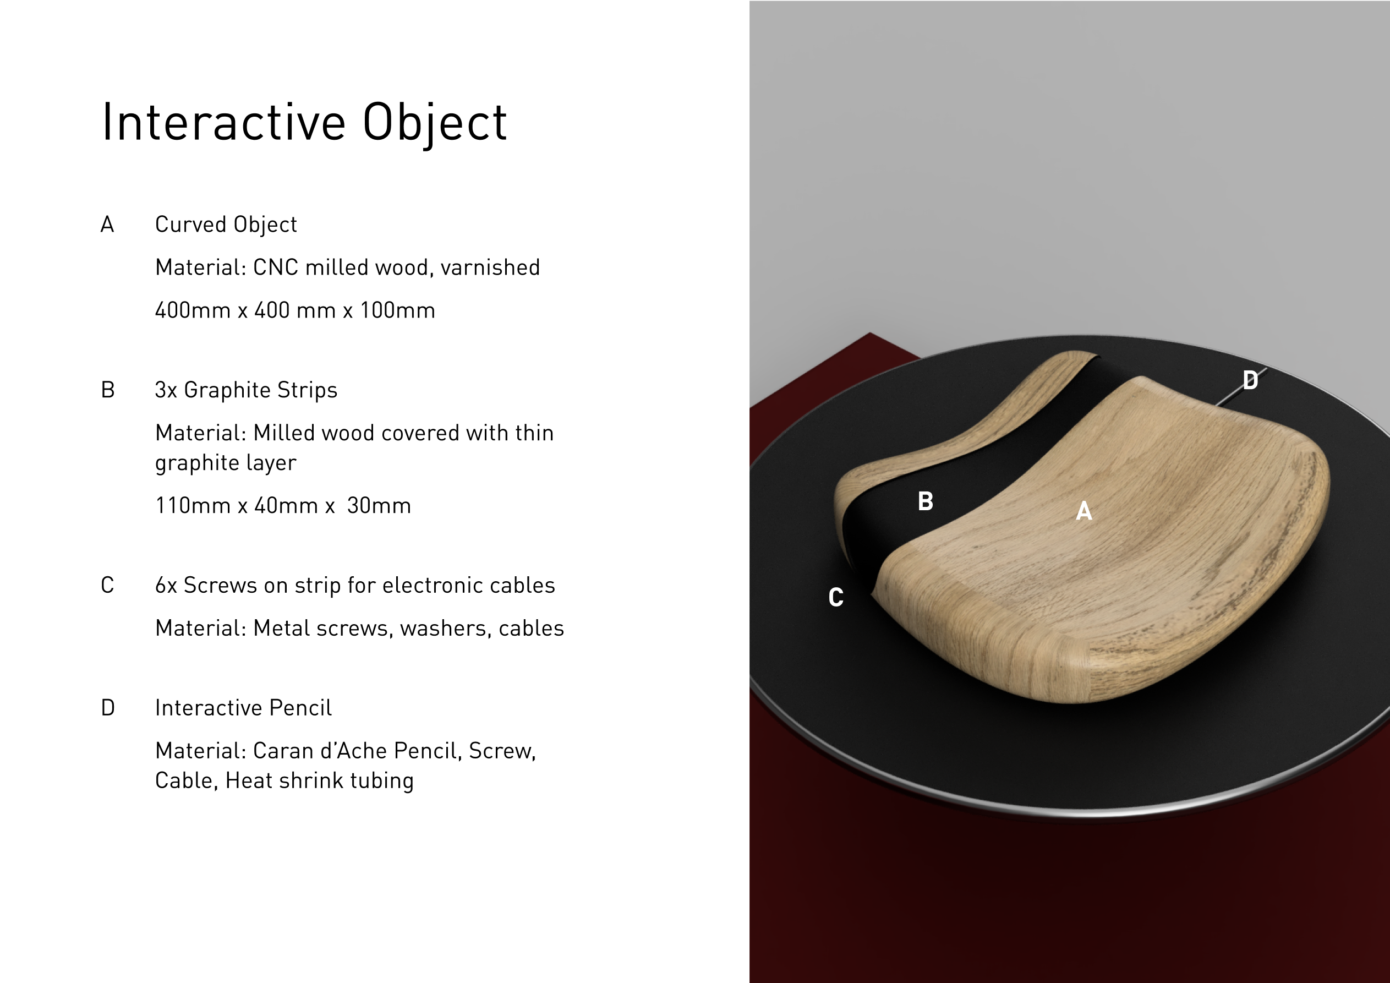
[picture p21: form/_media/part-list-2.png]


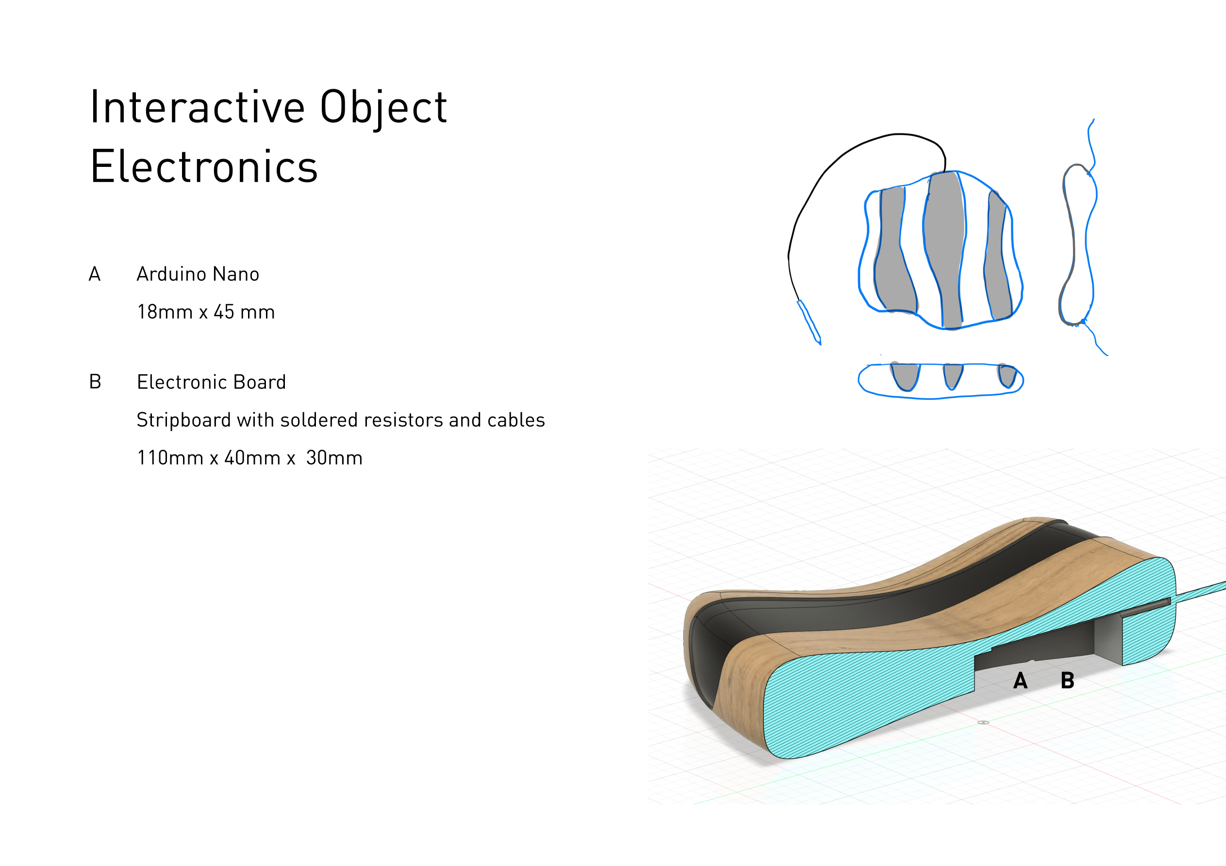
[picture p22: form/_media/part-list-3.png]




## Old Version Part List

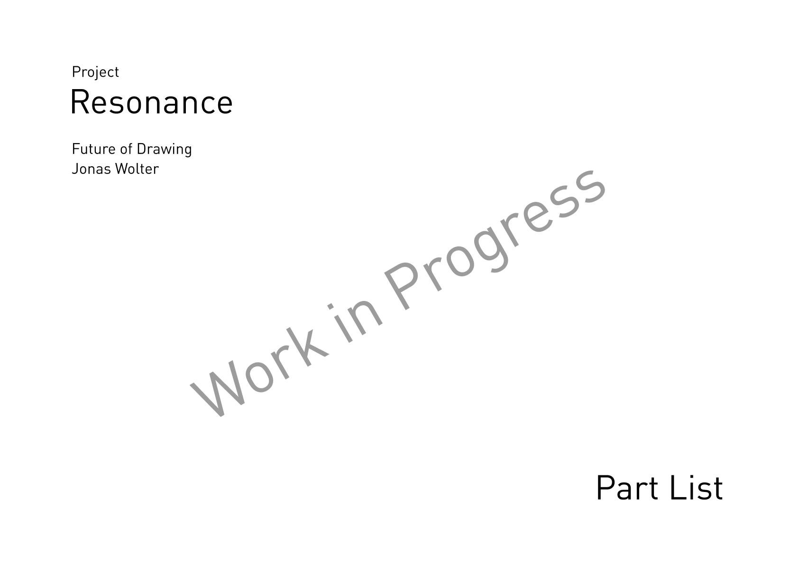
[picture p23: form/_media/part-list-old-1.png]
  
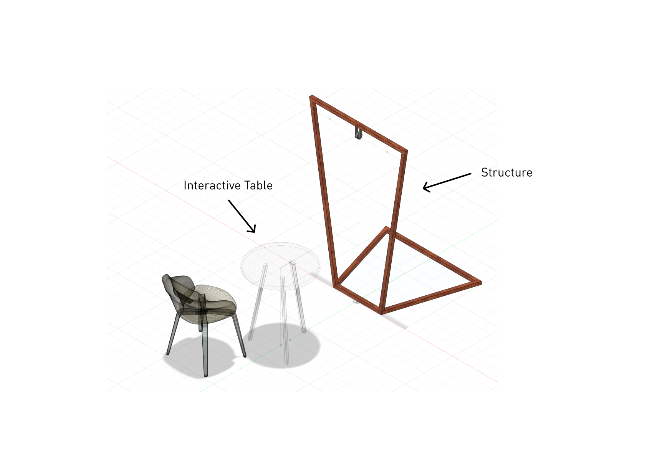
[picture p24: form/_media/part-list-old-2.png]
  
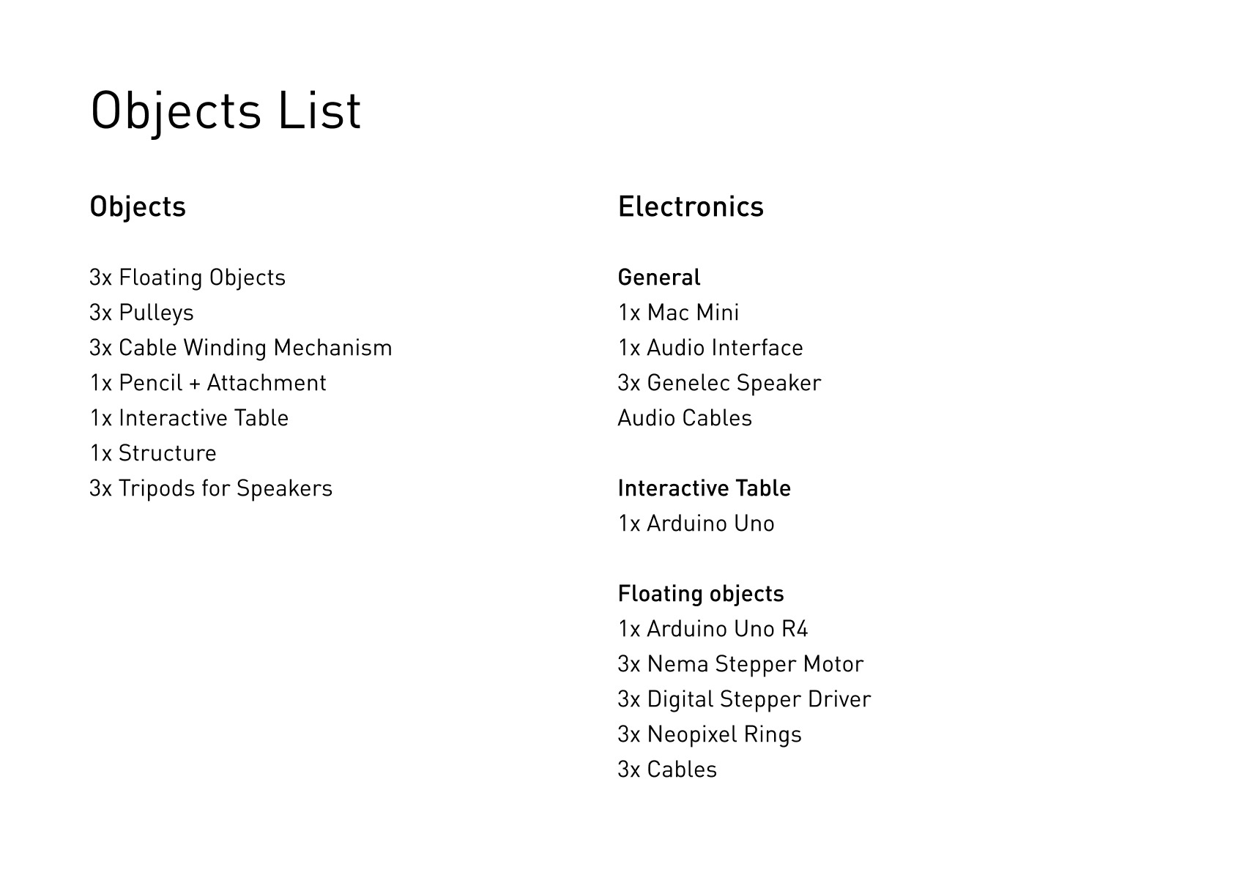
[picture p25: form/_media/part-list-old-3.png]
  
  


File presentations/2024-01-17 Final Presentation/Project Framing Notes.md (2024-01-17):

# Project Framing Notes

A collection of random notes regarding the framing of the project and project description.

## Old Pitch

**Resonance**

The project « Resonance » creates a multisensory contemplative  
drawing experience, with the goal of grounding people.

<span style="color:rgba(244,63,94,1)">People interact with a mechanical drawing device that at the
same time gives constraints and sparks satisfaction through mo-
vement. </span>While drawing, electromagnetic measurements of the  
graphite scratching the surface are measured and transformed  
into sounds that are altered by an AI to create looping spheric  
<span style="color:rgba(244,63,94,1)">relaxing</span> sounds.

<span style="color:rgba(245,158,11,1)">The installation creates a feedback loop in which the person in-
fluences the soundscape through their drawing movements
while at the same time being influenced in their drawing by the
sound. </span><span style="color:rgba(99,102, 241,1)">Through this feedback loop a state of resonance
evolves.</span>

## Notes

Resonances and sound have a long tradition in religion, spiritual meditations, and alternative medicine for healing.  pop-culture, youtube helaing sound videos, therapy

mixing the healing movements of drawing, with the healing properties of resonating frequencies

Get to yourself through sound

sound / music therapy / meditation

resonate with soul

Form inspired resonance body, inspired by sound bowls

Modern interpretation of a sound bowl

Resonance objects

Resonance bodys

harmonic resonance

resonate

body awareness

energy flow

body-mind connection

looking at the stars

zen mode / meditation

taming your inner mind

visitor is invited to get into a state of resonance, practically as well as metaphorically

through the rhytmic drawing movments visitors enter a state of resonance with the room as well

both literally with the space and metaphorically with yourself.

"grounding" difficult

finding inner balance, stability, Serenity

cognitive / mental balance

centering, anchoring, earthing

<span style="color:rgba(99,102, 241,1)">contemplation</span>

spiritual, transcedent

healing frequency

self-care, self-healing

find your body frequency

- Sensory play
- Exploration of the senses

Drawing is not a process, drawing is movement

calming experience

Drawing as an act of movement

focus on drawing as claming form of movements

multisensory exploration

using the movement of drawings as a way to get into a healing resonance with yourself.

> Diese Instrumente sind in der 432 Hz Frequenz gestimmt, welche aus hinduistischen und buddhistischen Traditionen stammt. Im Vergleich zur westlichen Welt ist dort statt 440 Hz die 432 Hz Stimmung der Standard.Denn es wird angenommen, dass sie in besonderer Weise unsere Chakren, die Lebensenergiezentren, anregt und dadurch spirituelles Erwachen fördert. Healing Frequency Handpans zählen zu Instrumenten mit besonders langem Nachklang, die wir für meditative Erlebnisse und Klangreisen empfehlen. Auch die Healing Frequency Serie hat ihren ganz eigenen Charakter. Diese Instrumente zeichnen ihr besonderes metallisches Design sowie eine feine Klangfarbe aus.
> 
> [handpan.world](https://www.handpan.world/de-ch/collections/healing-frequency)

Soundscape journey

Sonic odyssey

harmony voyage

> In an age where stress and anxiety are all too common, the simple power of sound therapy presents a remarkable opportunity for restoration and balance. In an age where stress and anxiety are all too common, the simple power of sound therapy presents a remarkable opportunity for restoration and balance. 
> 
> [ouraring.com](https://ouraring.com/blog/the-benefits-of-the-9-solfeggio-frequencies/)

Artist Quotes

> Color is the keyboard, the eyes are the harmonies, the soul is the piano with many strings. The artist is the hand that plays, touching one key or another, to cause vibrations in the soul.
> 
> [Wassily Kandinsky](https://www.brainyquote.com/authors/wassily-kandinsky-quotes)

**Bioresonanz**

> In der Bioresonanztherapie geht man davon aus, dass jedes In der Bioresonanztherapie geht man davon aus, dass jedes **Lebewesen ein eigenes Energiefeld** hat. Innerhalb dieses Feldes kommunizieren Organe, Gewebe und Zellen miteinander - über Schwingungen. hat. Innerhalb dieses Feldes kommunizieren Organe, Gewebe und Zellen miteinander - über Schwingungen.
> 
> Ziel der Bioresonanztherapie ist es, die Schwingungen wieder ins Gleichgewicht zu bringen und Störungen zu eliminieren.  Ziel der Bioresonanztherapie ist es, die Schwingungen wieder ins Gleichgewicht zu bringen und Störungen zu eliminieren.  Ziel der Bioresonanztherapie ist es, die Schwingungen wieder ins Gleichgewicht zu bringen und Störungen zu eliminieren. 

### Resonance

The interaction as well as the link to the "instruments" got much clearer today. I consider the keyword "Resonance" as the main keyword for the installation. "Resonance" can be interpreted in a metaphorical way, e.g. finding your inner resonance / get grounded as well as in a physical way for the interaction. Inspired by the mechanics of a pendulum or swing the goal is to make pencil movements in a specific rhythm to get into resonance with the oscillating floating objects which are hanging in the back. Similar to a physicial pendulum you can not just apply force at any time, you have to find the right moment to get the pendulum oscillating. The movement of the three pendulums will then influence the sound.

### Design Process

I was inspired by the calming nature of drawing movements. Focus on abstract drawings instead of figurative ones.

<span style="color:rgba(99,102, 241,1)">Slow Rhythm</span>

Experiments with the goal of increasing the multisensory perception of drawing

- drawing barefoot in the shower
- blindfold drawing
- meditation, one drawing per breath

At the same time started to gain interest in the rich electromagnetic properties of graphite, initial idea from random card drawing experiment.

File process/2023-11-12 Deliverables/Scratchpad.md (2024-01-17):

and the emphasis shifts to the act of drawing while the actual form becomes irrelevant.

Visitors are encouraged to go with the flow

go with the flow instead of drawing figurative

The act of drawing and feeling gets center stagem while the actual drawing looses focus

You don’t draw to have a drawing. Throug drawing you paint with sound. The drawn line gets a new meaning.

and the AI is altering the the

the installation uses the repathing breathing rhythm of meditation and the the analogue richness of graphite. to create white noise inspires sounds.

audio looping

By combining the slow repating rhythm of meditative breathing with the infinite analogue richness of graphite

a sounscape evolves

By entering barefoot and starting to draw

As soon as the visitors enter the room barefoot and start drawing the

where people have to walk barefoot into as the floor is coverd

The visitors enter barefoot into a puristic, dark room, the floor of which is covered with water and in which only a hanging pencil in the centre of the room and a paper ceiling on the wall can be seen.

Visitors barefootedly a purist dark room which floor is covered by water in which only hanging pencil in the middle of the rooom and blanket of paper on the wall can be seen.

helps people ground themselves.

Drawing from my research about methods people start

analogue richness is used to manipulate sounds.

Sound that builds up like a looping machine.

Starting from like a looping machine.

Drawing from my research on the

Inspired by the conductive properties an experience is mad that can help people ground themselves

by an AI. Starting from an purist setting of a dark room with only

in a room which floor is filled with

meditative pulsating painting of sound and light, in tacit dialogue with an AI.

cocreation with an AI
which is influenced by an AI.

in silent dialogue with an AI

the analogue richness of graphites electromagentic conductivity is used to express

in which

sound and light

in whichthe conductive

electromagnetic properties of graphite are used to create a painting of sound and light.

in which visitors can ground themselves.

of graphite are used in conjunction with.

by using the conductive properties of graphite
electromagnetic

In my project I want to create an contemplative drawing experience. Drawing from my experiments with meditative drawing settings I want to creat

In the contemplatative drawing experienc

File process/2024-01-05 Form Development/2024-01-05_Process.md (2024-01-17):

# 2024-01-05 Process

Form Research



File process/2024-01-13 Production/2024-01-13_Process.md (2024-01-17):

# 2024-01-13 Process

Prototyping the equipment box for computer, sound cards and projector



Producing the pencil cap



Ableton sound design work in progress



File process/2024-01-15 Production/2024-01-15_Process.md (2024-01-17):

# 2024-01-15 Process

**CNC Machining**

Finally the CNC started producing the piece. However due to the size of the object the production will unfortunately take until tuesday. The file takes around 10 hours to produce. 



**Installation Table / Equipment Box**

I produced the table today. I am very happy with the practical design. Walls can be easily removed and put again to have easy access to the tech equipment. 

[Video of the modular equipment box design](IMG_0768.mov)



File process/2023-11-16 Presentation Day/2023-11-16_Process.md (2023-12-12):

# 2023-11-16 Process Log

Today was the big presentation day to show our current state of the work to Caran d'Ache. Sophie from the marketing departement of Caran d'Ache was present and gave us feedback on our projects. 
My presentation can be found in the folder [presentations](/presentations/).

## Official Feedback after presentation

- Can you find an physic response to the drawing in addition to the sound?
- Positive feedback from Laure about the form of the object
- Could the machine also directly be an instrument? Could the things moving up and down generate the sound?
- Look into people doing gong experimentations, a lot of videos online.

## Other feedback
- one persone thinks the current project still kinda looks like a torture machine (you torture the pencil for your own well-being)
- another person pereceives the apparatus more as a sculpture that would be interesting to look at while it moves independently. More inviting to look at than to interact by yourself. 

## Observation

During the day I observed many people of our class independently walking to the prototype and trying it out just out of curiosity. There definitely seems to be some appeal or attraction to the object.

  
Spotted people randomly trying out object

## Log / Reflection

I felt quite stressed the days before the presentation. Tuesday evening I had bit of a existential crisis with the project. But after an discussion with pablo I found a way to move forward. The new idea and prototype I came up with is not perfect and I had quite a critical feedback with Alexia and Douglas on Wednesday evening. However there are some interesting things about it even though I will have to refine / rethink a lot. I accepted that this is a work and progress and not the most elaborate idea yet. The presentation went well and I am now much more relaxed afterwards. The general feedback from Douglas and Alexia after the presentations was reassuring. In the evening I had a discussion with Douglas that helped a lot with the understanding of the project and imagination of next steps.

## Feedback with Douglas after classes

- Quite contradictory feedback: Very critical feedback from Douglas & Alexia on wednesday evening. Good feedback from Sophie from Caran d'Ache and good feedback from Laure. 
- Douglas relativated Alexias critique, especially as there was also positive feedback today. I definitely don't have to throw away the new object, but still also have to explore pure graphite interactions without the new object. 
- It's okay when the topic of grounding also evolves, for example change into something like "floating". 
- It's totally okey if there is no AI inside it. 
- Douglas / Alexia are pushing us to simplify things to really get to the core of the interaction. But it doesnt have to stop there. Once we have that core we will add recomplexify later in the process.
- Thinking the object as an instrument doesn't mean its only mechanical. There is also a world of physical digital soundmaking. Douglas showed very interesting reference projects of the german artist Moritz Simon Geist, see below. 

## Reference Projects of Moritz Simon Geist

Vibrations  
https://www.youtube.com/watch?v=F_h4LO-8Uxg

Feature Ring  
https://www.youtube.com/watch?v=lduN5rsHovI

Sonic Robots  
https://vimeo.com/sonicrobots

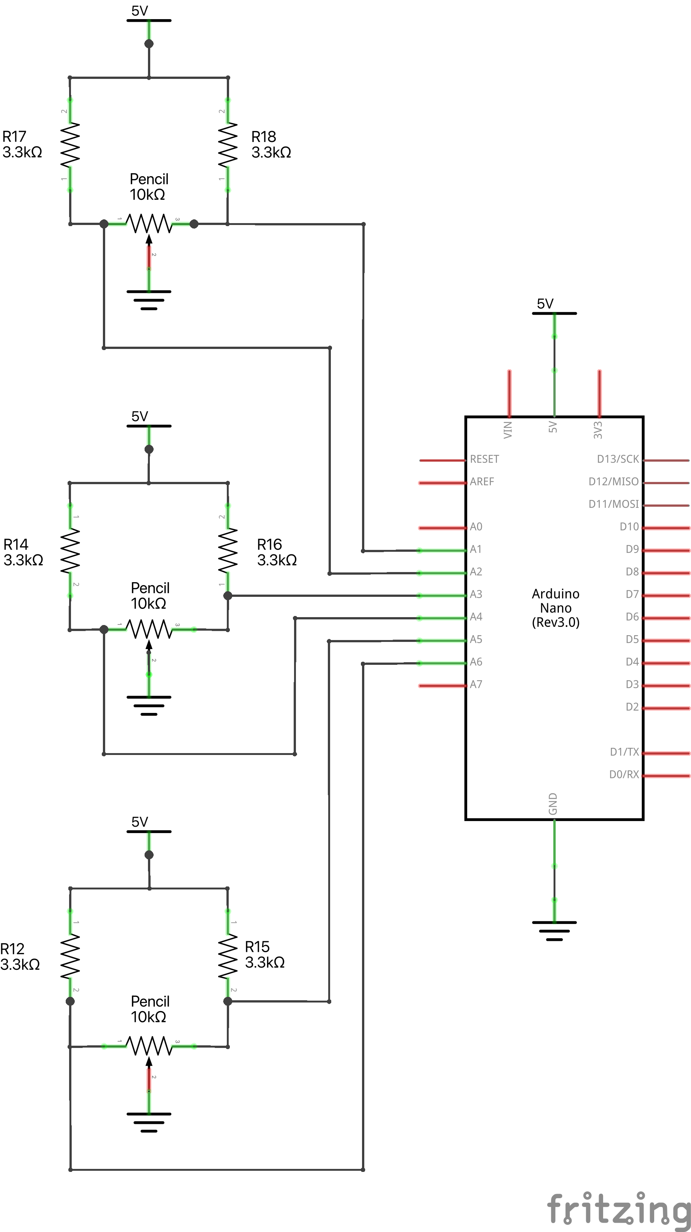
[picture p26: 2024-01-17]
electronics/fritzing/Arduino Nano 4_schem.png

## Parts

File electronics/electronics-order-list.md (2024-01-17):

# 2023-12-05 Electronic components order list

- Nema Step-Motors & Drivers & Flange Couplings
- Long thin flexible cables
- Colored LEDs
- camera / distance sensor
- mechanical belt?
- 

Other Material

- Plastic foil
- metal plate
- 3D printed parts

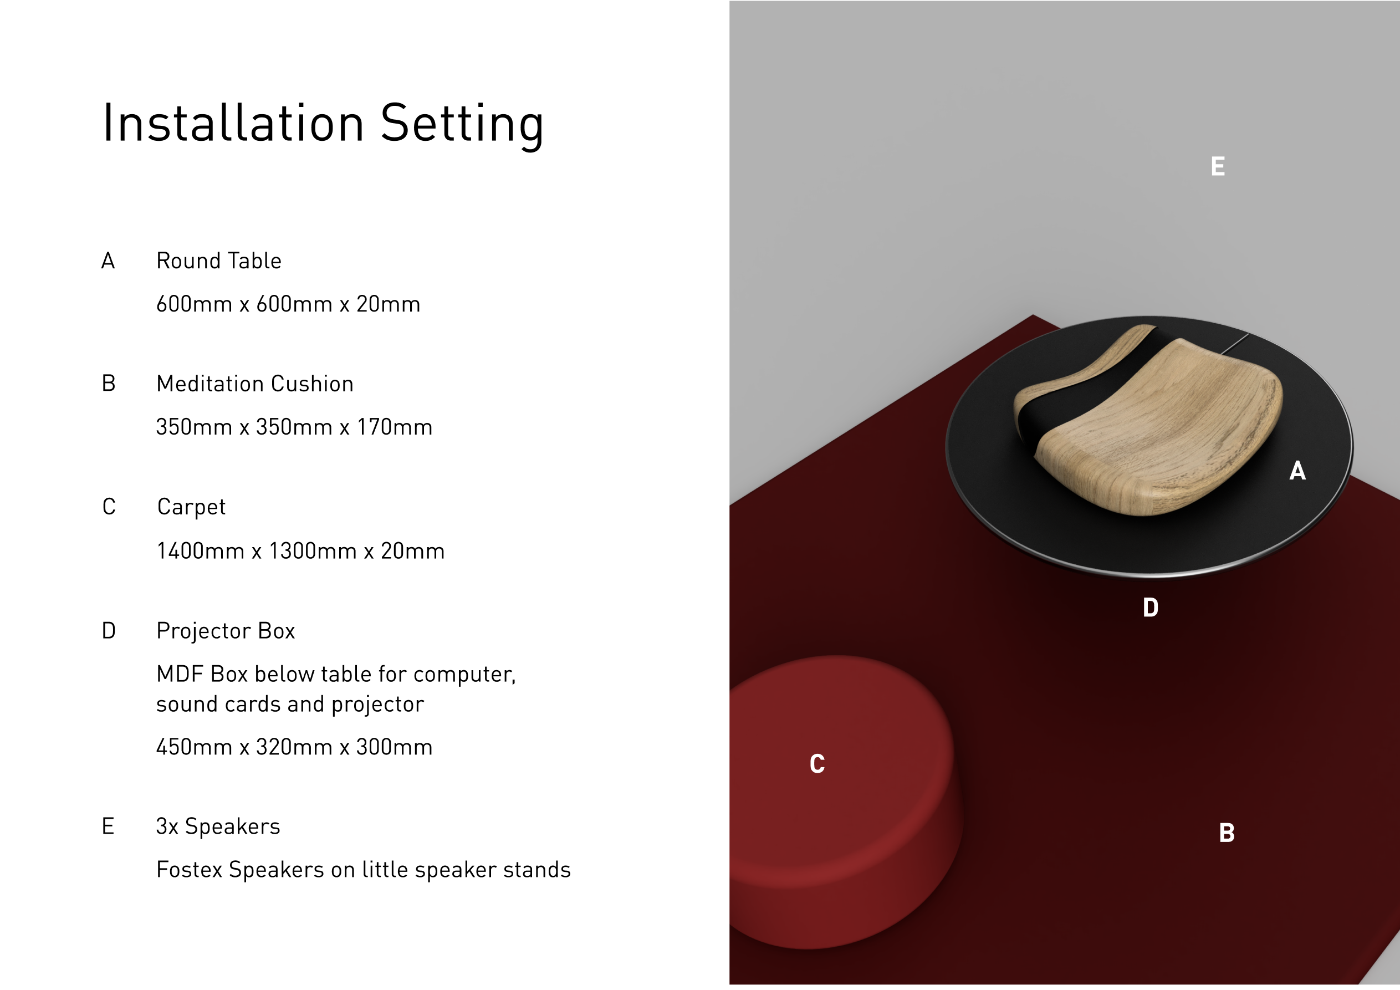
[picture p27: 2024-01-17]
form/_media/part-list-4.png

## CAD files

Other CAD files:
form/fusion/Installation Sketch v1.f3d
form/fusion/Installation v1 v6.f3d
form/fusion/Installation v2 v8.f3d
form/fusion/Installation v3 v3.f3d
form/fusion/Installation v4 v3.f3d
form/fusion/Installation v5 v7.f3d
form/fusion/Tutorial 1 v2.f3d
form/fusion/Tutorial 2 Soda Bottle v5.f3d

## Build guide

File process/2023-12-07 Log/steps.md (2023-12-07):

# All the steps to builld the thing

## Form

- More paper sketches
- Decide on final form
- 3D Modeling (Fusion 360, maybe also Rhino for room setup)
  - Floating objects
  - Cable winding mechanism
  - Cable routing / pulleys
  - Interactive table / pillar (pencil & metal plate interaction)
  - Pencil cable attachement

## Materials

- Plastic 3D prints (cable winding mechanism, floating neopixel structure)
- Wood / metal / plexiglas for interactive table structure (tbd)
- Metal or carbon plate for interactive plate on table
- Plastic foil / paper for floating objects (tbd)
- Fasteners for electronics and wiring

## Electronics

**Arduinos**

- Arduino 1 (metal plates sensor)
- Arduino 2 (stepping motors controller)

**Inputs**

- Metal plate resistance measurement (only arduino and electronics needed)
- Distance sensor or camera (backup if position measurement over resistance is not accurate enough)

**Data processing / Sound synthesis**

- Windows or Mac computer for TouchDesigner & Max Msp

**Outputs**

- 3 stepping motors for the 3 floating objects (Nema Motors & Motor Drivers)
- Neopixels inside floating objects
- 3 speakers (preferred Genelec)

**Code**

- Arduino code for resistance & position measurement
- Arduino code for motor & neopixel control
- TouchDesigner sketch for kinetic and light interaction
- Max Msp patch for sound processing

**Power supply**

- AC to DC converters for arduinos
- computer power supply
- speakers power supply

**Wiring**

- Long, thin and flexible power / data cables on which floating objects with neopixels are attached to
- Long enough USB cables for connections between arduino and computer
- fancy cable for pencil
- electric power cables
- audio cables

**Dimensions**
- ?? (tbd -> need exact room dimensions for that)

**API**

- [optional] maybe sound synthesis AI if not done with classical generative methods

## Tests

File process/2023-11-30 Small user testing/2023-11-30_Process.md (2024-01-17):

# 2023-11-30 Process

Today we had 3D classes with Laure. Next to learning the new 3D softwares I improved my prototype and added an Max Msp sketch to synthesize sounds based on the resistance measurement of the pencil. I tested the prototype with a few persons of our class. 

## User Testings

[Video of the prototype](IMG_0318.MOV) 

[Video testing](IMG_0308.MOV)

**Feedback**
- interesting interaction, makes fun to play with
- sound is too annoying with time and does not have enough changement yet
- no reaction to pencil position yet

**Conclusions**
- Interesting path, interaction is generally working, but I have to go again more into the concept. I want to research more into the topic of musical and metaphorical resonance.

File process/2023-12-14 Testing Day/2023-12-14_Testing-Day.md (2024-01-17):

# 2023-12-14 Testing Day

## General objective

Test the quality of the resonance interaction (rhythmic pencil movements to get floating object oscillating).

## Testing setup

I prepared a first coded prototype for today. By moving the pencil on an wood plate covered by a thin layer of graphite the testees can add or remove energy to the vertical pendulum which is projected on the wall. There is no direct interaction (e.g. directly applied pencil position to position of the floating object) but an indirect interaction where the energy of the oscillation can be changed through pencil movements.

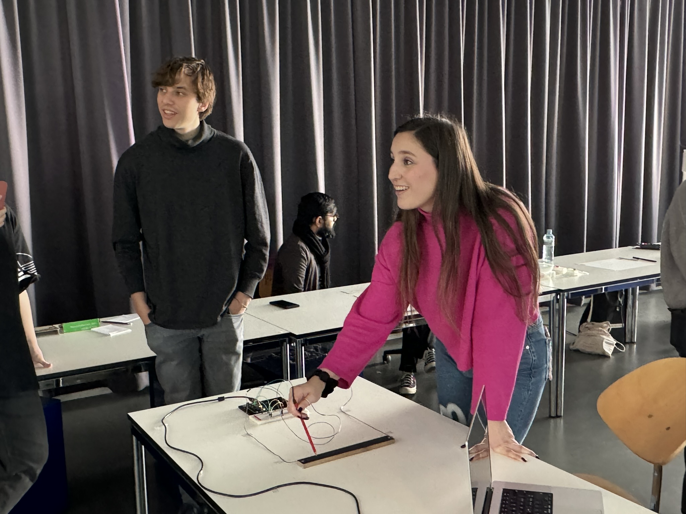
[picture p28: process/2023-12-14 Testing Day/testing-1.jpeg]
  
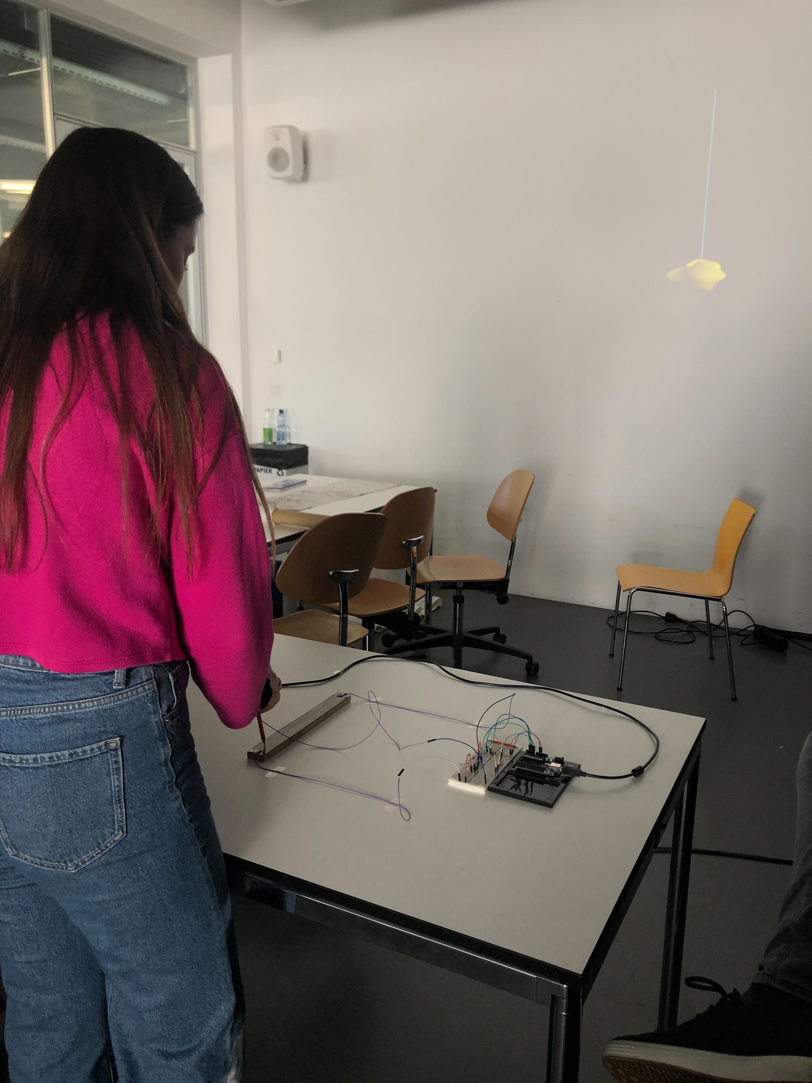
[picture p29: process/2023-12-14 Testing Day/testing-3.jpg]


## Testing questions

- Do people understand the (indirect) interaction without instructions? How long does it take them to get the concept?
- Can the interaction last for several minutes or does it get boring fast?
- Is a setup where people sit or a setup where people stand better suited for the installation?
- A/B-Testing: Slow moving object (low sensitivity) vs fast moving object (high sensitivity). How do they compare to each other?

## Testing results / feedback

- Speed and sensitivity matters a lot for interaction! In testing A with a slower oscillation (and therefore greater delay) speed people didn't understand the indirect interaction concept of adding and remvoving energy. However in testing B the people understood the concept after some time of trial and error.
- People were attracted by the interaction. The interaction time was much higher than in all my previous prototype tests.
- More guidance needed for interaction! Testees were intrigued once they got the concept, but they might cancel if they don't get the interaction. (especially outside of this test setting)
- It was unclear what the goal of the interaction is. When I gave them the task to try to get the object oscillating as high as possible, it got clearer.
- even though the interaction plate was long but narrow, people still tried to do horizontal movements
- people reported that the plate was too narrow resulting in less comfortable movements
- people much prefer to sit during interaction instead of standing due to a more comfortable hand drawing pose
- should it be a very personal and closed setting (maybe with headphones or ASMR sounds) or a public setting, where others can watch?
- Colored Light: Different light colors can help to better understand the interaction, but the current yellow activation light is confusing. The colors don't have to be on the moving object. They can also be somewhere else in the room.
- One person perceived the floating object as a living being and described the indirect interaction as "taming the animal"
- not much (emotional) attachement to the floating object yet
- every time I try to explain the concept of "grounding" people do not easily understand it

## Conclusions

- The big importance of a faster speed means that the whole scale of the installation depends on the power and smoothness of the motors that I ordered. If they don't have enough power I need to decrease the movement distance of the floating objects, which severly impacts the general scale of the installation. It is a big difference for the scale whether objects can only move 20cm up and down or if it's 1.5 meters. This unknown complicates my planning and physical production.
- People want to sit. This changes my phsical setting.
- Do there have to be 3 different plates for each object or can I use one larger plate to interact with all of them?
- Think more about the setting (shared vs personal)
- Explore how I can improve the guidance to get people to understand the interaction faster
- Think about whether marked zones of oscillation height with corresponding sounds might be interesting (for example by putting physical colored strings)
- maybe interesting keywords for project framing: taming your inner mind, zen mode

## Talk with Pablo regarding scale

- Go for smaller scale, safer & quality of interaction matters. This means not attaching the floating objects to the ceiling but building my own support structure.
- Always better to have something working good in a small version and then make it larger for the exhibition
- When I put the floating objects nearer to the person they appear bigger in relation

## Interaction Table

- Probably it does make sense not to build the whole table on my own for the Januar presentation, but reuse an existing one and only build an interaction pult on top of that.
- Together with Pablo I went to the basement to checkout existing material. The black MDF table on the picture below might be an interesting option.

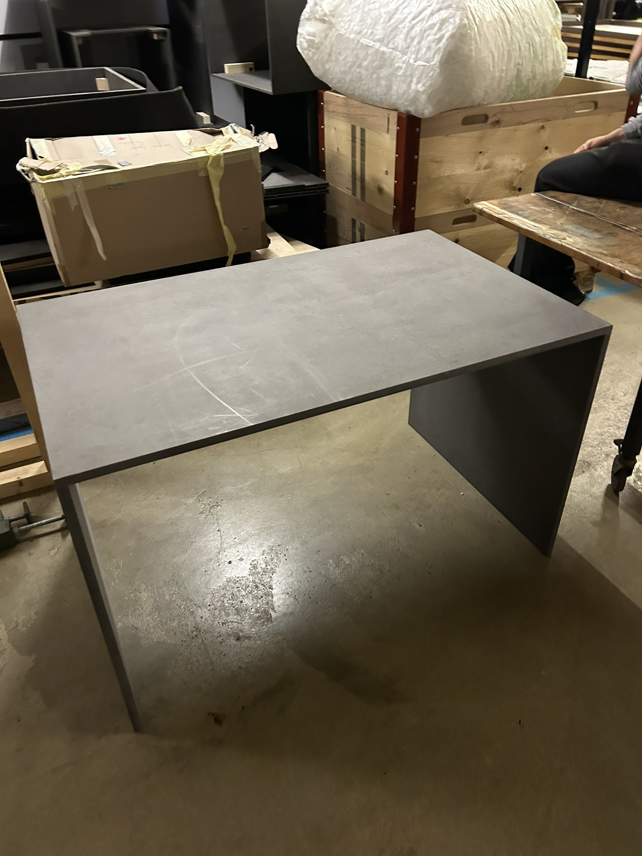
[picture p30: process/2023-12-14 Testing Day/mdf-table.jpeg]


## Sound Design Thoughts

- Volume of sound and complexity should be depending on amplitude. In non-moving idle state there is no sound.
- Maybe different height thresholds trigger different sounds
- Rhythm of oscillation creates rhythm of sound

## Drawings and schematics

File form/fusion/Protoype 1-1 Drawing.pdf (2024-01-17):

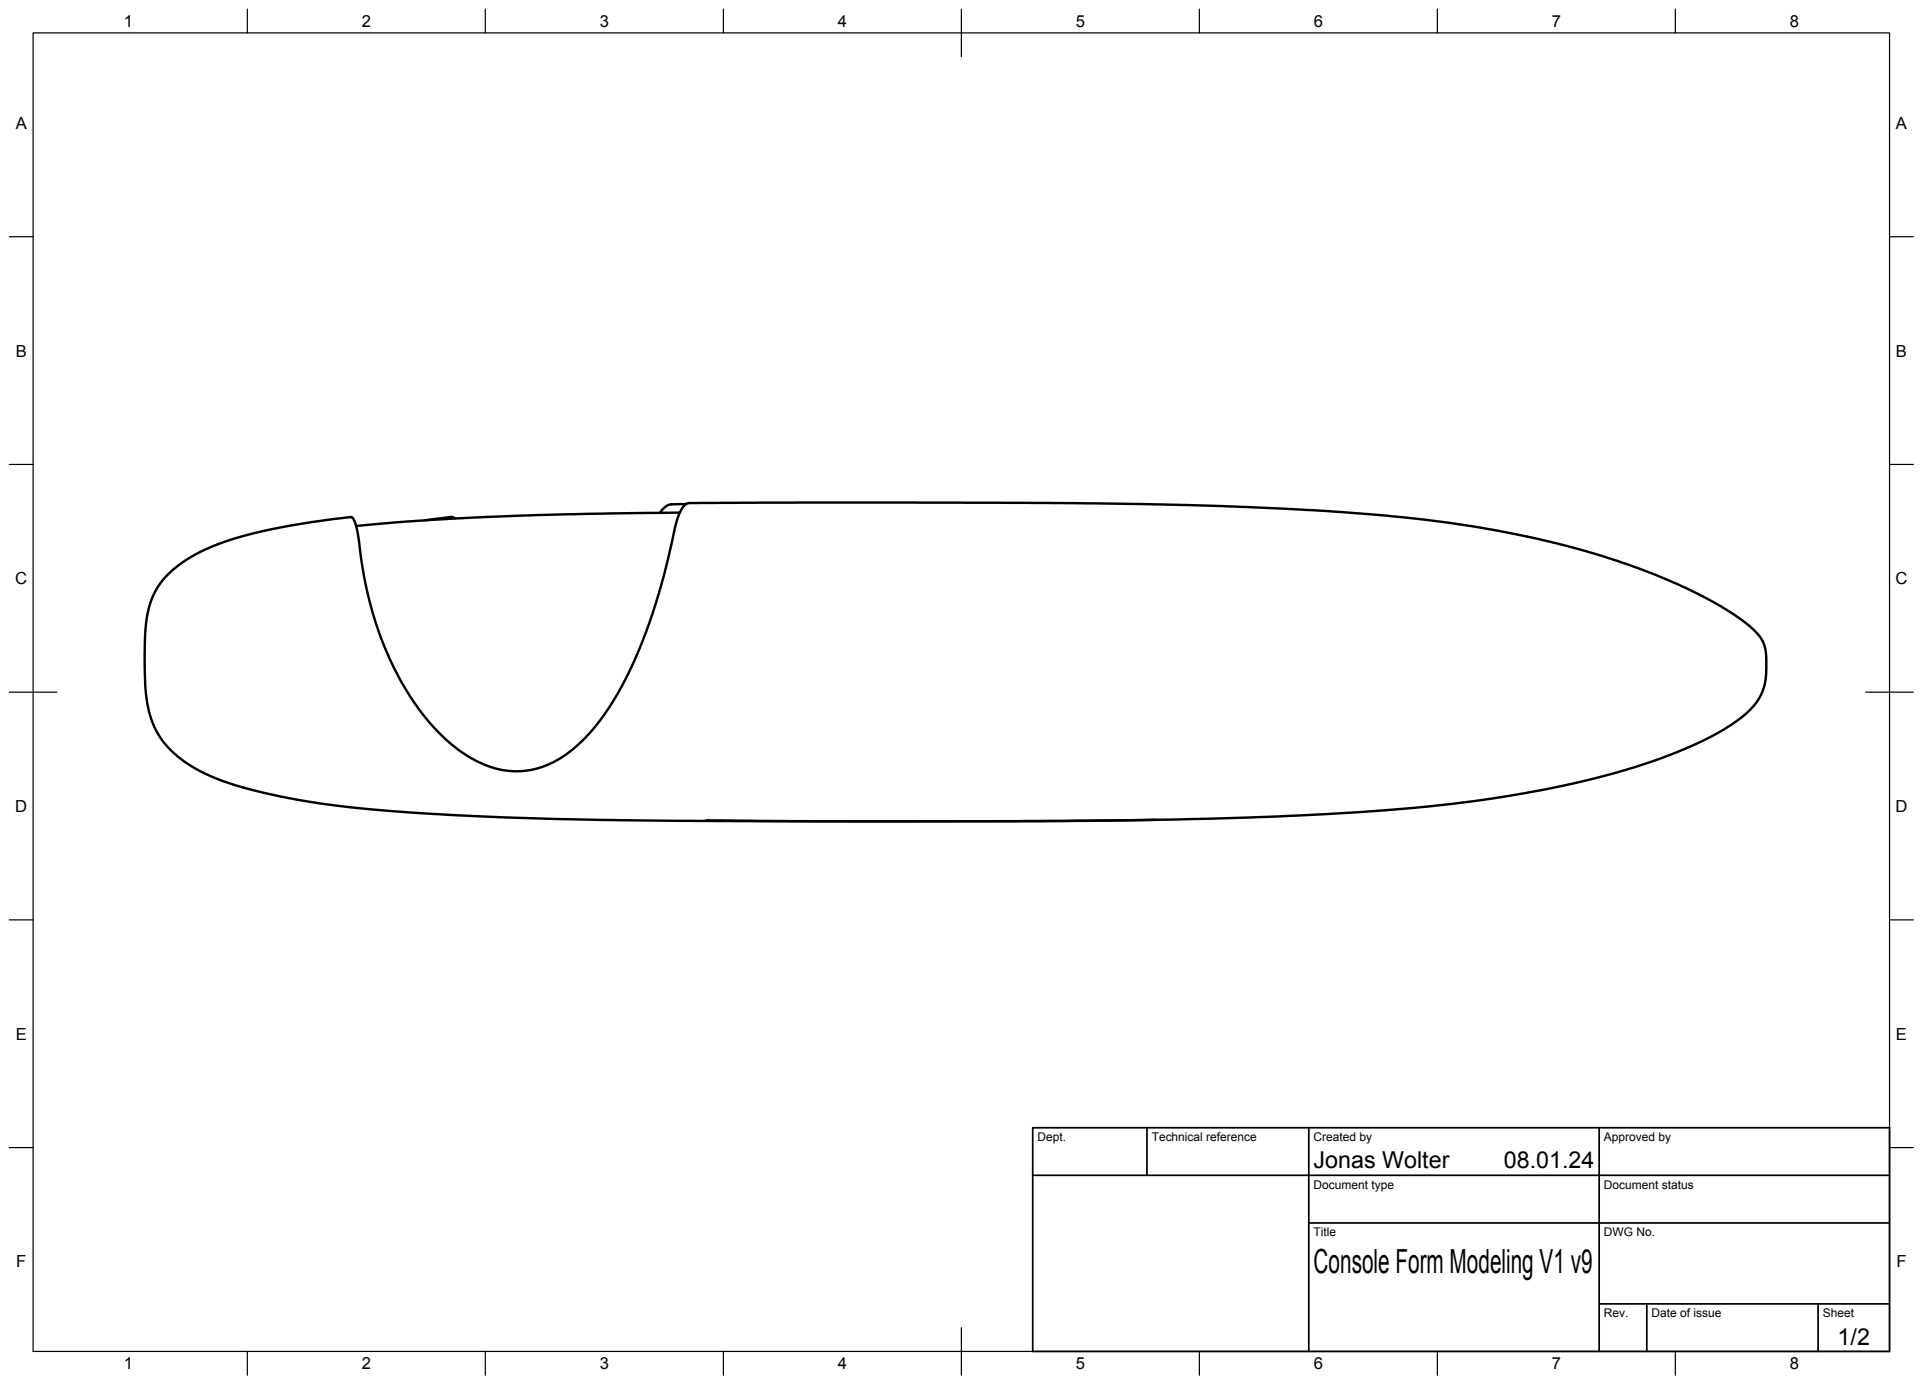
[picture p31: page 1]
Title; DWG No.; Rev.; Date of issue; Sheet

Dept. | Technical reference | Created by Jonas Wolter 08.01.24 | Approved by

Document type | Document status

Console Form Modeling V1 v9

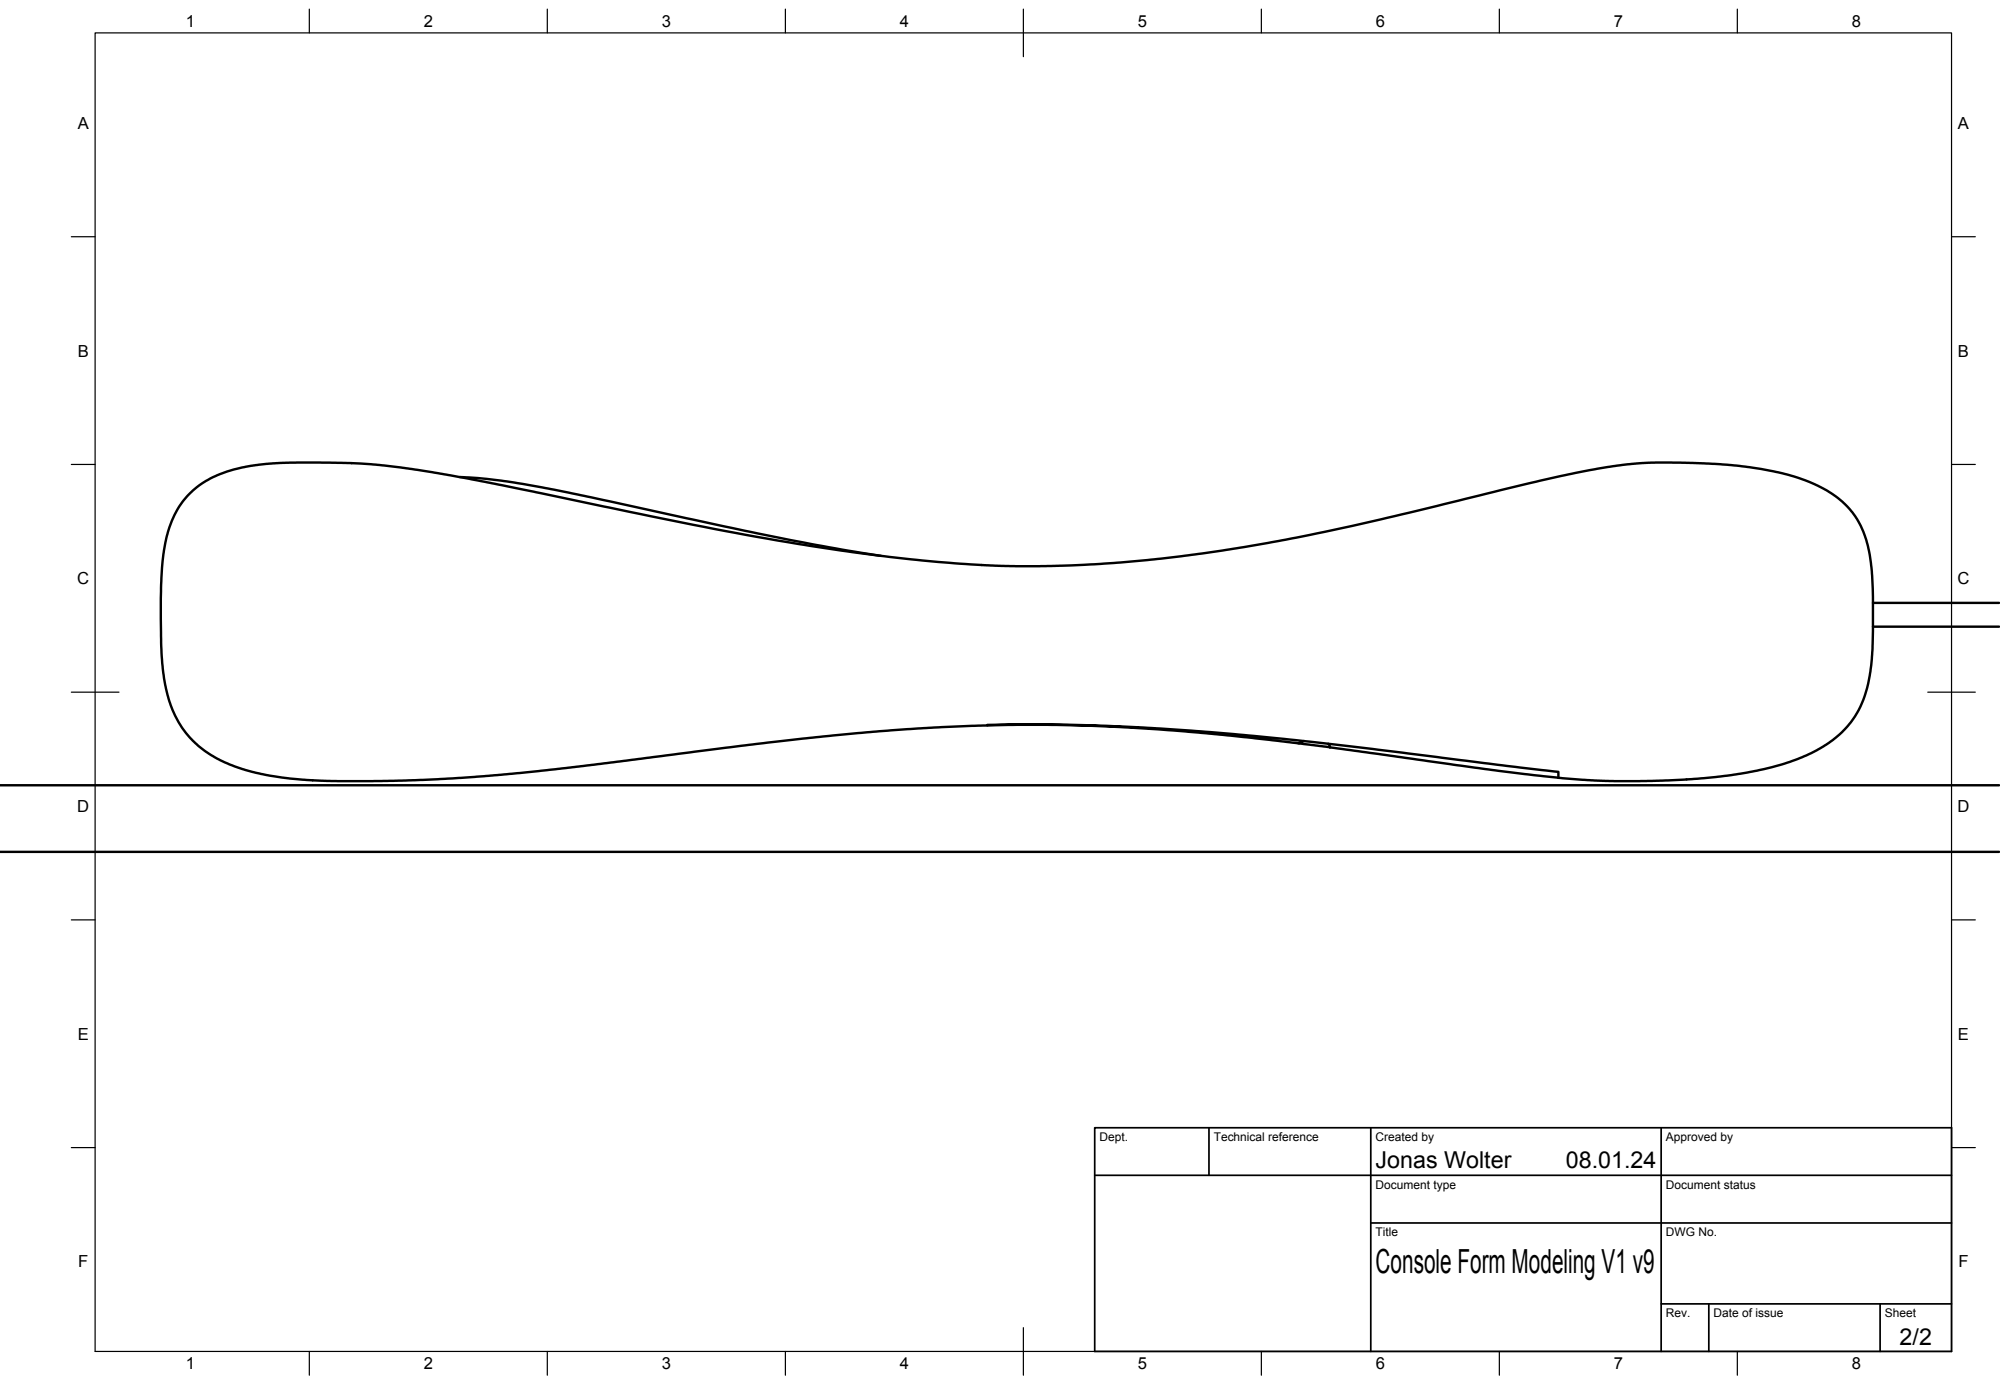
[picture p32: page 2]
Title; DWG No.; Rev.; Date of issue; Sheet

Dept. | Technical reference | Created by Jonas Wolter 08.01.24 | Approved by

Document type | Document status

Console Form Modeling V1 v9

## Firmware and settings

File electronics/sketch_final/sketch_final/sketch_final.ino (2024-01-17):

const int numChannels = 6;
int rawValues[numChannels];

void setup() {
  delay(1000);
  Serial.begin(38400);
}

void loop() {
  for (int i = 0; i < numChannels; i++) {
    rawValues[i] = analogRead(i);

    Serial.print(rawValues[i]);

    if (i < numChannels - 1) {
      Serial.print(",");
    }
  }

  Serial.println();
}

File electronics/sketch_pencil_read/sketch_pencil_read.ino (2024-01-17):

int raw1 = 0;
int raw2 = 0;
int raw3 = 0;
int raw4 = 0;

void setup(){
  delay(2000); 
  Serial.begin(38400);
}

void loop(){
  raw1 = analogRead(1);
  raw2 = analogRead(2);
  raw3 = analogRead(3);
  raw4 = analogRead(4);
  Serial.print(raw1);
  Serial.print(",");
  Serial.print(raw2);
  Serial.print(",");
  Serial.print(raw3);
  Serial.print(",");
  Serial.println(raw4);
}

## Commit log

2023-11-13 Add 2023-11-13 Deliverables (Pitch, Research, User Journey, ...)
2023-11-17 Add 3D rendering files for prototype
2023-12-12 Update Electronics folder
    [pencil-measurement-amplified.fzz, pencil-measurement.fzz, soldering-exercise.fzz]
2023-12-14 Update touchdesigner, max & node js programming
    [pencil-measurement-amplified.fzz]
2024-01-17 push all local
    [Arduino Nano 2.fzz, Arduino Nano 3.fzz, Arduino Nano 4.fzz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]
